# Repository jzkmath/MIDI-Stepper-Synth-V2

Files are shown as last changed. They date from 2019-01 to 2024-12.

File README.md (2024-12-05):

# MIDI-Stepper-Synth-V2
This is the Version 2 of my MIDI Stepper Synth. The key differences between this and Version 1 is
that this version uses the Terasic DE0-nano (Cyclone IV) FPGA as the controller instead of Arduino.
The key advantage to doing so is that an FPGA can execute commands at the same time instead of sequentially.
This also allows for a better understanding of how MIDI actually works, because the MIDI has to be decoded manually
instead of using a MIDI library.

This project is being performed at the Virginia Tech AMP Lab, and the project can be seen (Link is dead)

Alternatively, you can view the project documentation/Notes in the "Project Documentation" folder and opening the "Documentation.md" file.

**Please use the project page or PDF to see the BOM and all information on this project!!!**

Since MIDI uses a specific type of UART, the FPGA will take the serial data and convert it to parallel, as a 3 byte register.
Once this is done, the message is decoded such that the stepper motors react accordingly. 

## Basic MIDI Layout
The 3 byte MIDI Message is as Follows:
**1XXXCCCC 0NNNNNNN 0VVVVVVV**
- **X** - MIDI Command. This is 1000 for Note OFF, and 1001 for Note ON.
- **C** - MIDI Channel. 
- **N** - MIDI Note. This is the pitch that is specified. 60 for example is Middle C or C4.
- **V** - MIDI Velocity. This is similar to volume.

The general idea is that we want to turn the MIDI value into a stepper speed. To do this, we use a
similar method to how version 1 handles this, except this time we use clock cycles instead of time.
The DE0-nano has a 50 MHz clock, so we can generate a square wave at a specific frequency by counting
a certain number of clock cycles and toggling the state of a pin. 
The code simply takes the MIDI note value and converts it to the corresponding number of clock cycles
needed to do so.

In addition to the functions of version 1, version 2 also uses the velocity information to control 
how many steppers turn. The higher the velocity, the more stepper motors turn on (ranging from 0-4)
This is how the array of floppy drives work on the popular "Floppotron" on YouTube.

## Block Diagram
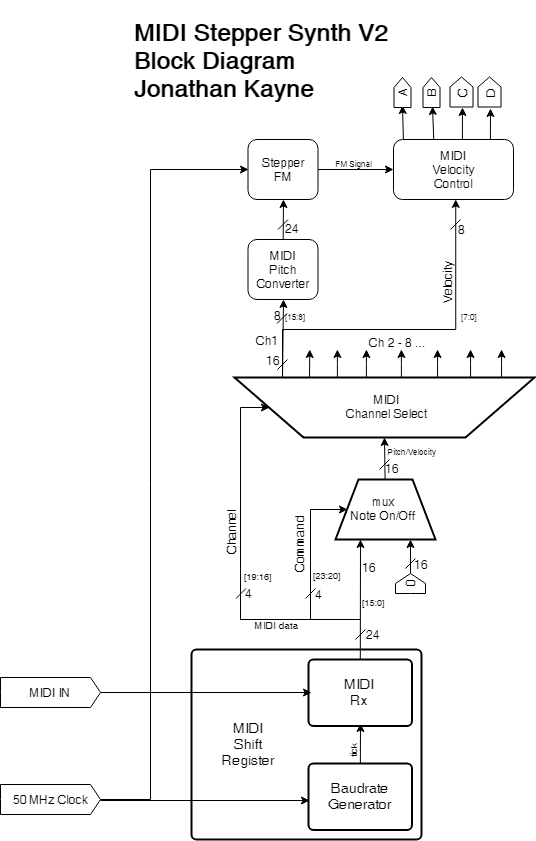
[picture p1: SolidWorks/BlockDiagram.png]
Block Diagram


## Principle of Operation
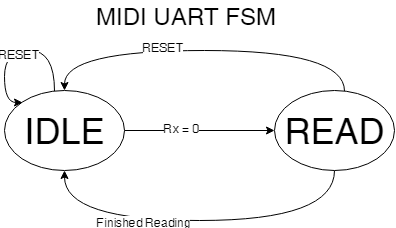
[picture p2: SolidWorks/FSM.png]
FSM


The first thing that must be done to convert MIDI into stepper music is that we need to decode the MIDI signal. MIDI uses 31250 baud UART (Universal Asynchronous Recieve Transmit) to send an recieve data. This is a form of serial, so we need to load this into a register to act upon with combinational logic. To do this, we use a Finite State Machine, or FSM with two states; Idle and Read. 
In the Idle state, the Rx line is high. When a device wants to send a message, the Rx line is dropped low. This is known as the start bit and the actual data is the 8 bits that follow, then the line goes high again (called the stop bit).

Knowing this, we can use the start bit as a means to change to the read state. 

In the read state, we want to look at the Rx line in the middle of each bit and shift that bit into our register. To do this, we count a certain number of clock cycles to get to the center of the bit. Given that the DE0-nano has a 50MHz clock and MIDI is 31250 baud, that means that it takes 800 clock cycles to get to the center of a bit, and 1600 clock cycles to go from center to center.

When the start bit is detected the read process is as follows:
1. count 800 clock cycles to get to the center of the start bit
2. count 1600 clock cycles to get to the center of the data bit
3. shift in the value of the Rx line
4. repeat steps 2 and 3 a total of 8 times
5. output the shifted value
6. wait for the Rx line to go high (stop bit detected) and go back to the Idle state.

Once we do that, we have our byte of data. Knowing that MIDI is 3 bytes of data, we take the byte and shift it into a larger, 3 byte register. After that, we can use combinational logic to control the stepper motors.

MIDI has a byte of control information (Command and Channel) and two bytes of data (Pitch and Velocity). We want to use the first byte to properly route the last two bytes appropriately. To do this, we have a single data router module and register modules for each channel. The registers have an enable and clear control signal and will either load or clear their contents depending on which input is pulled high. The second and third bytes are connected to the inputs of all the registers via a common bus and the first byte is used by the router module to control which register gets enable or clear pulled high. Note on (1001) or Note Off (1000) determines whether the register is enabled or cleared, and the channel determines which channel this happens to.

Once the register has the data, we need to convert the pitch into clock cycles. We look at the pitch value and corresponding frequency. We then figure out how many clock cycles elapse in half the period of the note. We do half because we want to create a square wave, which has a 50% duty cycle.

Using the converted value, we have a module count up to that value and then toggle the state of the pin. This is the equivalent to the "Blink without delay" sketch that is used in Arduinos (except for FPGAs).

Finally, we use the velocity value to determine how many stepper motors get that signal, which can be anywhere between 0 and 4.

## Credits
The basic UART decoding Verilog code is based off code provided by Electronoobs, modified to be more stable and work with MIDI.

Special Thanks to Robert Perkel and Bob Lineberry for helping with this project and providing assistance with this.

## Legal
This project is under the GNU GPL3.0 Open Source License. 
You are free to use the code in your project, so long as you credit the creator (Jonathan Kayne).
I want people to be able to use my code, but I don't want people to plagiarize my work!

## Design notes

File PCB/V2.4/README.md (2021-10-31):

### Stepper Synth V2.4

This is the Final Revision of the MIDI Stepper Synth V2 PCBs. They were designed in Eagle, and rendered in KiCAD.

I added new connectors and changed the header sockets to be in a zigzag pattern so that they would be easier to solder.

## Interface PCB
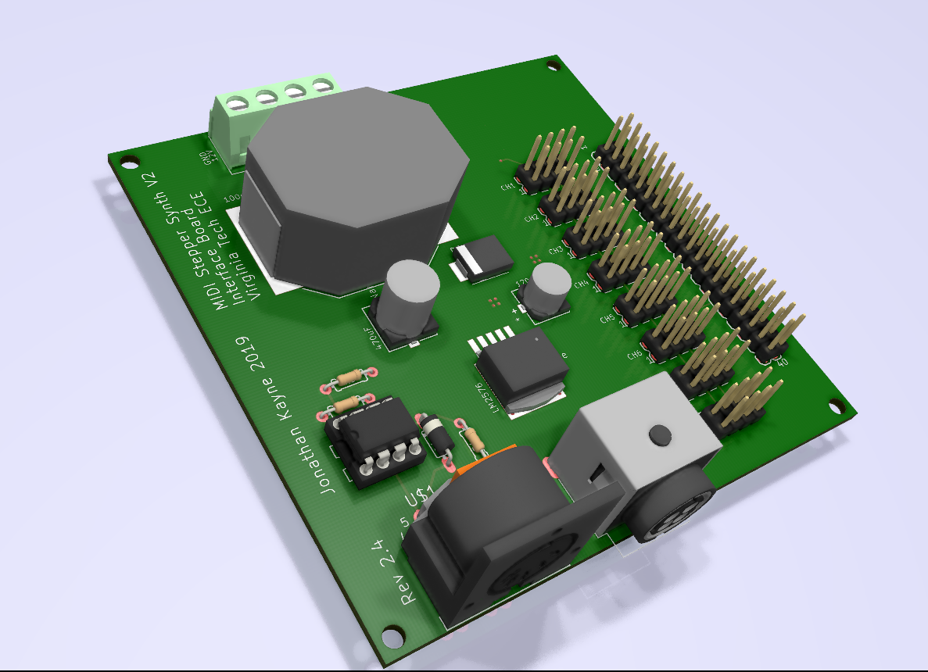
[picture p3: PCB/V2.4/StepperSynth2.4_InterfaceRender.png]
Interface


## Motor PCB
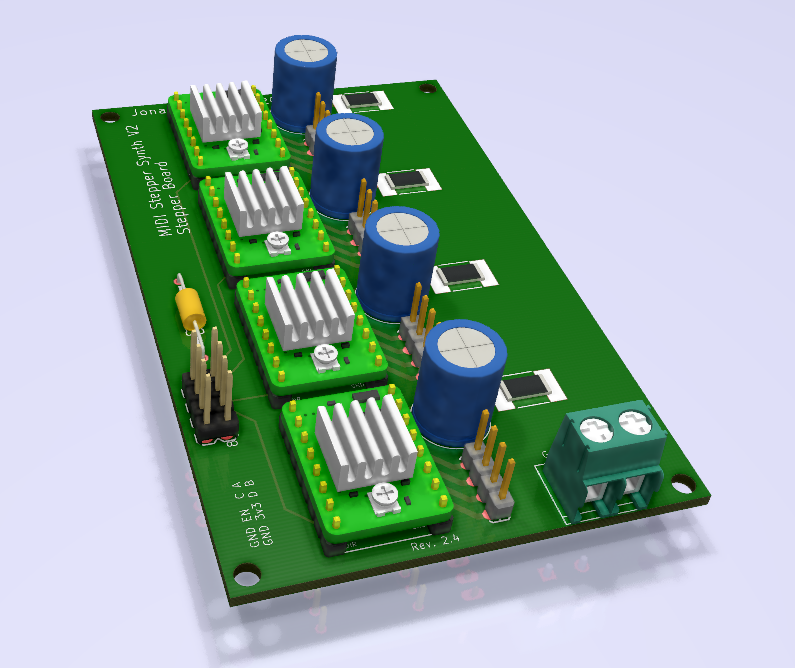
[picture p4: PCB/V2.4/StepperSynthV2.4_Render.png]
Motor


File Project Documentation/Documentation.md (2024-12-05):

# MIDI Stepper Synth V2

## By: Jonathan Kayne, Virginia Tech Class of 2021

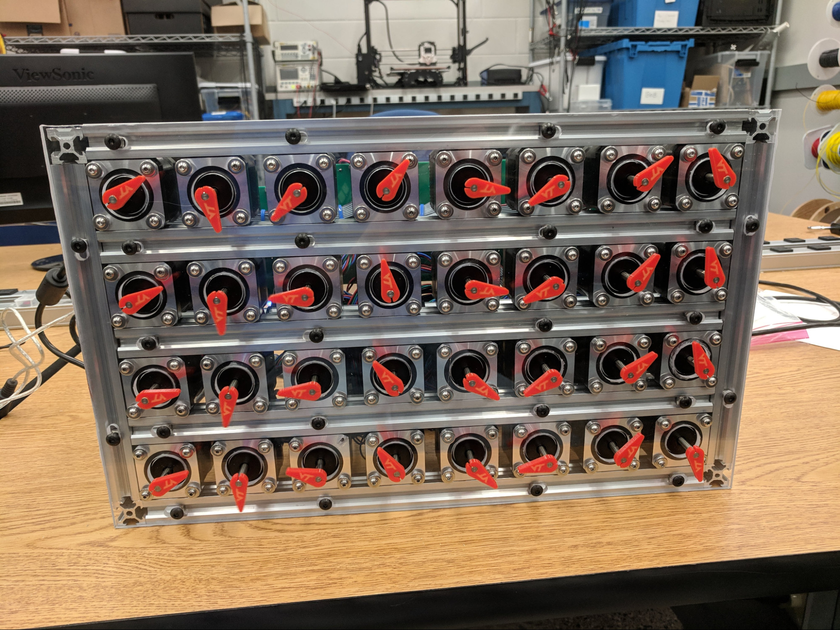
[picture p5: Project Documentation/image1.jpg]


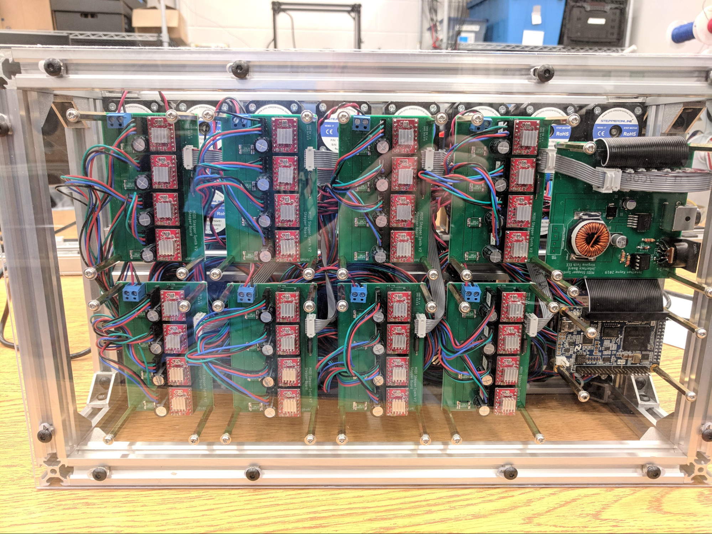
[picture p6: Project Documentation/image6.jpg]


## Project Overview

This will be a continuation of a project I designed in the spring of 2018 on my own. The stepper synth uses MIDI data to "Play" stepper motors. Stepper motors often create a hum that is dependent on the speed that the motor is spinning at. By writing music and sending it to the stepper synth, you get a song. The original stepper synth used 4 NEMA-17 Bipolar stepper motors, an Arduino Uno, and a CNC shield to drive the steppers.

This design works, but can be improved by adding more steppers and other instruments. Furthermore, use of an FPGA will allow for a faster processing time and more stable MIDI processing.

Optionally, an array of LEDs could be used with some filtering to light up depending on the frequency being played at any time.

## Tasks

* Choose appropriate FPGA

* Come up with a plan for the program.

## Educational Value Added

I have very little experience in FPGAs and verilog. Doing this project will allow me to learn procedural verilog as well as get a more in depth view of the MIDI protocol.

## Design Decisions

The MIDI stepper Synth will use an array of 8x4 Bipolar stepper motors (likely NEMA 17). These will be broken into 8 MIDI channels with 4 motors per channel. Use of 4 stepper motors will allow for variation in volume level, by changing the number of motors running.

## Design Misc.

Other information about the design, parts used, etc.

* The stepper motors are driven by the Allegro A4988 Stepper Motor driver module. These drivers contain two main control pins; Step and Direction. Direction controls whether the motor spin clockwise or counterclockwise, and Step advances the motor forward by 1 step upon the rising edge of a pulse signal. The frequency of the pulses sent to the step pin control the speed at which the motor turns. It just so happens that the frequency also corresponds to the audio tone that the motor produces. For example, if I were to put a 440 Hz square wave into the step pin, the stepper would produce an A4 note (440 Hz is a common frequency used for instrument tuning!).
* Musical Instrument Data Interface (MIDI) is essentially a version of serial (RS232) at a specific baud rate. Within the protocol, there are two messages that we are concerned with; "note on" and "note off". These messages are 3 bytes long, and contain the control signal, the channel, the note value (frequency) and the velocity (volume).
* The general idea for what the FPGA needs to do is to take the midi data and produce a clock signal whose frequency is dependent on the note value. These signals need to be independent of each other and only get changed when another MIDI message overwrites it, so a note will stay the same until either a new note value is given or the note off message is received.

## Parts

* 32x NEMA 17 Stepper Motors
* 32x A4988 Stepper Motor drivers
* FPGA
* 3.3v to 5v level shifter (for communication between the FPGA and A4988)

## Steps documenting your design process

### Thing 1

The general idea of what this device does is takes MIDI data and converts that into a pulse whose frequency matches that of the stepper motor. To do this, the MIDI must first be interpreted and acted on accordingly.

MIDI is a special version of serial communication (RS232). It runs at 31250 baud.

MIDI will hold the signal high until a message needs to be sent. When this occurs, the line is dropped low for a single bit. This is called the start bit.

The MIDI messages we are interested in are 3 bytes in length. The Message is as follows: "CCCCNNNN 0KKKKKKK 0VVVVVVV" where

* C = Command; 1000 = Note OFF, 1001 = Note ON
* N = Channel; ranging from 0-15, for channels 1-16
* K = Note Value; the value 60 corresponds to C4 (middle C)
* V = Note Velocity; how loud the note is

The note value will drive the frequency of the pulses for a respective channel. The velocity will control how many stepper motors receive that pulse, where 0 = none, 1-31 = 1 motor, 32-63 = 2 motors, 64-95 = 3 motors, 96-127 = 4 motors. This might be changed if the range is too broad. It should be such that the motors respond to certain dynamic levels; from pianissimo (pp) to fortissimo (ff)

A midi channel does not change its value until another message overwrites it. So if a note on message is sent, that note stays on until either a new note on changes the value (creating a slur) or a note off message is sent.

The FPGA will have registers that hold the current note and velocity values for each channel. The data will come from a multiplexer that is controlled by the N bits. This is so the data that is loaded in can be routed to the appropriate register.

In the event of a note off message, the multiplexer will output a zero for both note and velocity.

If at all possible, an enable timeout feature should be implemented for the stepper motor control. The A4988 has an enable line that can be used to enable/disable the steppers. When enabled, the steppers have current supplied to them, which causes them to heat up (and waste energy!). When the device has been inactive for a certain amount of time, pull the enable line high.

### Thing 2

Information on the A4988 Stepper Driver. Here is a picture of the pinout for the A4988:

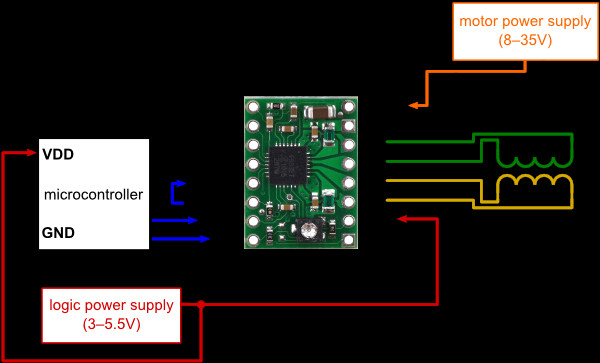
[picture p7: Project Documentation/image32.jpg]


The ENABLE line enables the driver when it is set to a logic low.

MS1-3 are the Microstepping mode controls. You can increase the resolution by changing the state of these pins (full step, half, quarter, eighth, and 16th). This doesn't matter for this project so they will be all driven low (full step mode). 

### (Preliminary Schematic)

**12/7/18:**  The schematic and board were created in Autodesk Eagle. The schematic and board are as follows:

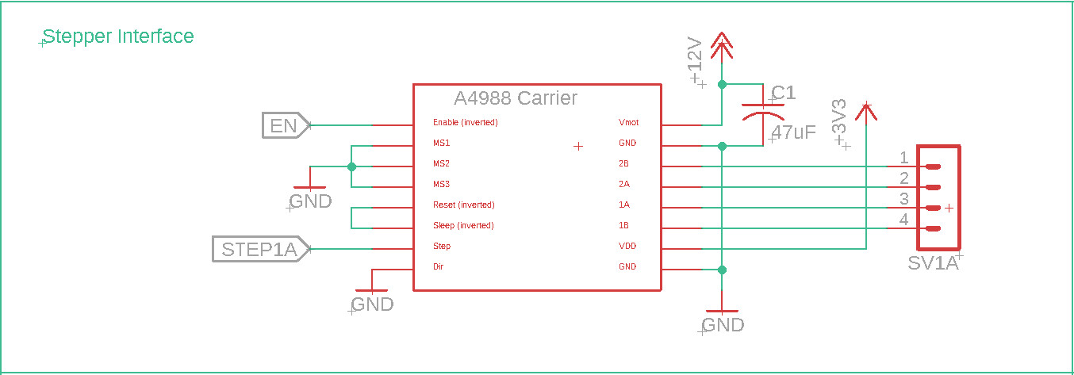
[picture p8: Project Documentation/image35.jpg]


The 47uF capacitor is there to prevent large voltage spikes from damaging the motor drivers. Looking at the Arduino CNC shield showed that each driver got its own capacitor.

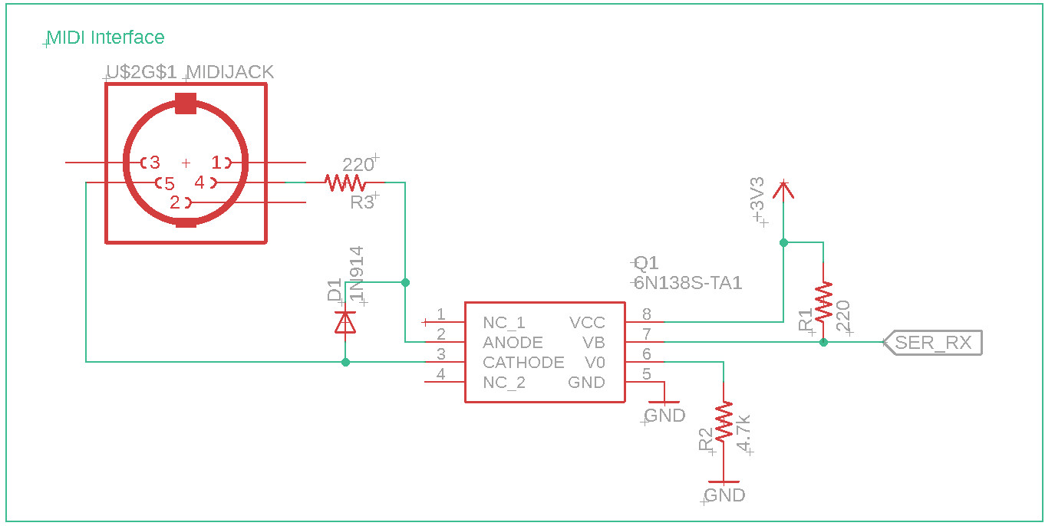
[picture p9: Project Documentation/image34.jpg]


The 6N138 is an optoisolator IC chip. MIDI uses a 5V communication method while the DE0 nano uses 3.3V. It is common to use an optoisolator to isolate the MIDI signal between the devices. It should also be noted that the ground connection on the DIN connector is left floating to prevent ground loops from occurring along the shield of the MIDI cable. The diode is for reverse polarity protection. The 4.7k resistor acts as a bleed resistor. This is due to the fact that stray charges can build up on the phototransistor, which can increase the propagation delay. The resistor fixes this. 

This is based off a tutorial by ["Notes and Volts" on YouTube.](https://www.youtube.com/watch?v=0L7WAMFWSgY)

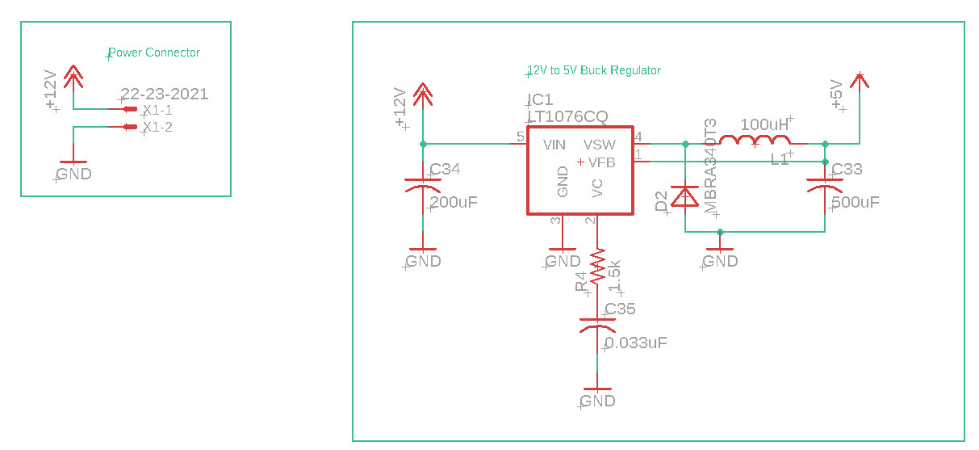
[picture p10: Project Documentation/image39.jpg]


This uses the LT1076 as a buck converter for converting the 12V to 5V to power the DE0 nano FPGA.

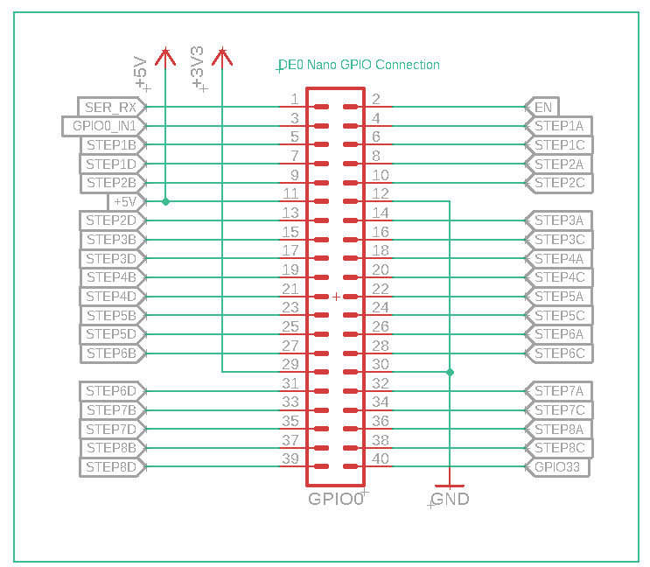
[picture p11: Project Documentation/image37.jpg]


## Verilog Works!
**12/13/18** - The Verilog code has been created and tested and now successfully works!

The main challenge to getting this to work was in the MIDI Shift Register, as MIDI uses a form of UART (Universal Asynchronous Receive Transmit). This means that there is no clock to keep things in sync. The solution is to use what is known as a Finite State Machine (FSM). The way the shift register pulls in data is done by creating a clock that is 16x faster than the specified baud rate (in this case 31250 bps) and then having two states: Idle and Read. The module sits in the Idle state until the serial line falls low, indicating the start bit. This puts the module into the read state. 

In the read state, the module counts 8 ticks (the clock that's 16x faster than our baud rate). At this point we are in the middle of the start bit. After this, we count another 16 ticks and record the value of the serial line. This is repeated for all the 8 bits, where the bits are shifted into a register. Afterwards, the module goes back into the idle state. 

Since there are 3 bytes of MIDI data, there is another shift register that shifts each byte in as it is received.  

After the bits are properly shifted in, the values are processed and sent where they need to be. The first thing that is analyzed is the command, which is either a note on (1001) or a note off (1000). The is a 2x1 multiplexer that either passes the pitch and velocity through if the value is a note on, and passes a zero through if the value is note off or anything else.

After that, the pitch and velocity go into a demultiplexer that sends the pitch and velocity to their intended MIDI channel. The specified channel is located in the last 4 bits of the first byte.

For each channel there are 3 modules: a pitch value converter, a frequency modulator, and a velocity controller. The pitch value converter takes the MIDI note value and converts it to a number that equates to the number of clock cycles needed for half the period of the intended frequency, since we want to produce a square wave. Since the clock is 50 MHz, you can calculate the number of clock cycles needed by 50 MHz / (2 * pitchFrequency). 

The converted value is then sent to the frequency modulator, which simply counts up to the specified number of clock cycles and toggles the state of a register. (essentially this is the same code used to blink an LED on an FPGA)

This signal is then sent to the velocity controller, which passes the signal to 0, 1, 2, 3, or 4 stepper motors depending on the velocity value given, where 0 is none, 1 - 31 is one motor, 32 - 63 is two, 64 - 95 is three, and 96 - 127 is four (all).

The block diagram is as follows. I have also added the verilog code, which is in the "files" section!

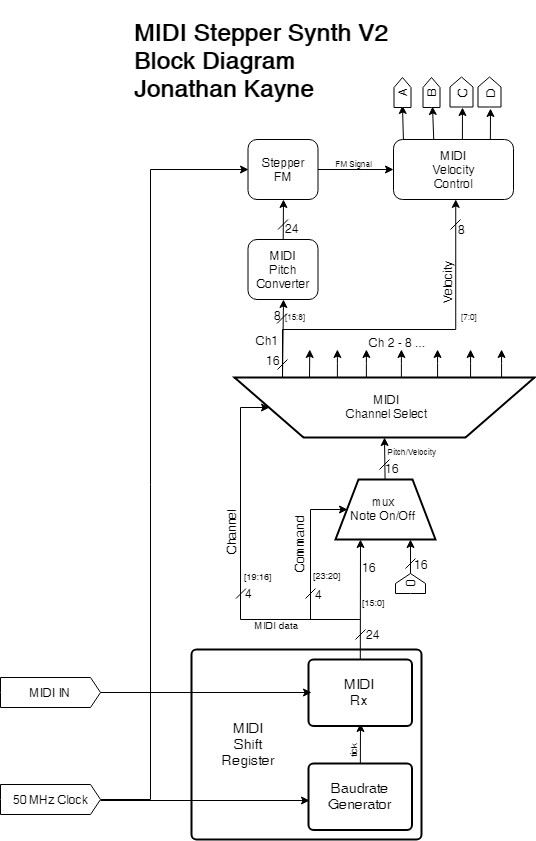
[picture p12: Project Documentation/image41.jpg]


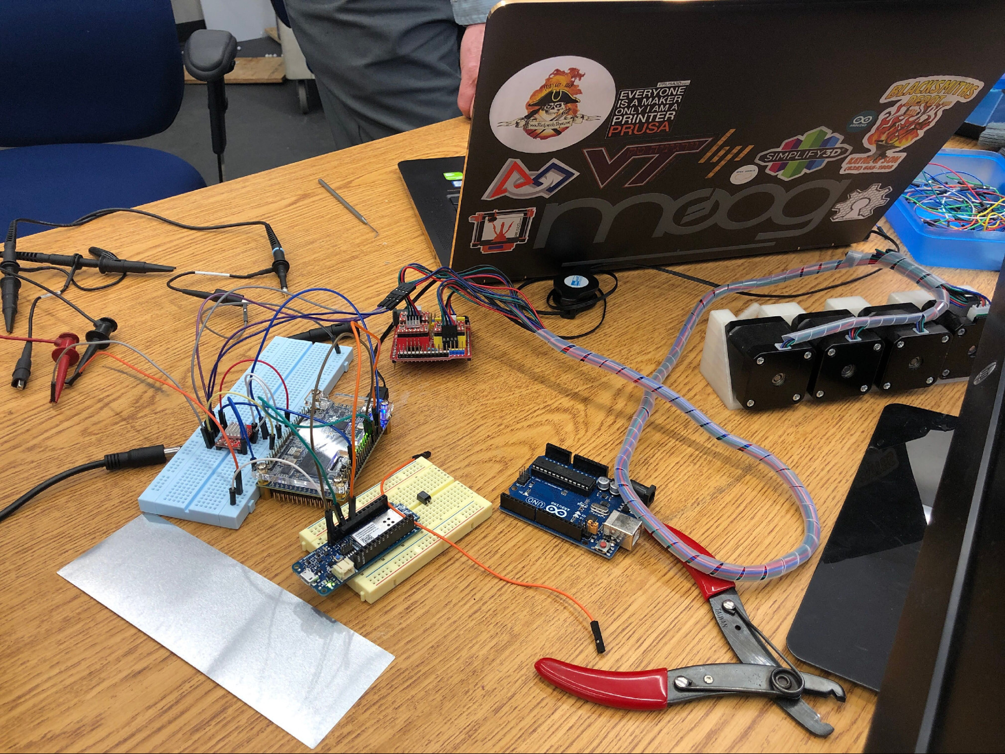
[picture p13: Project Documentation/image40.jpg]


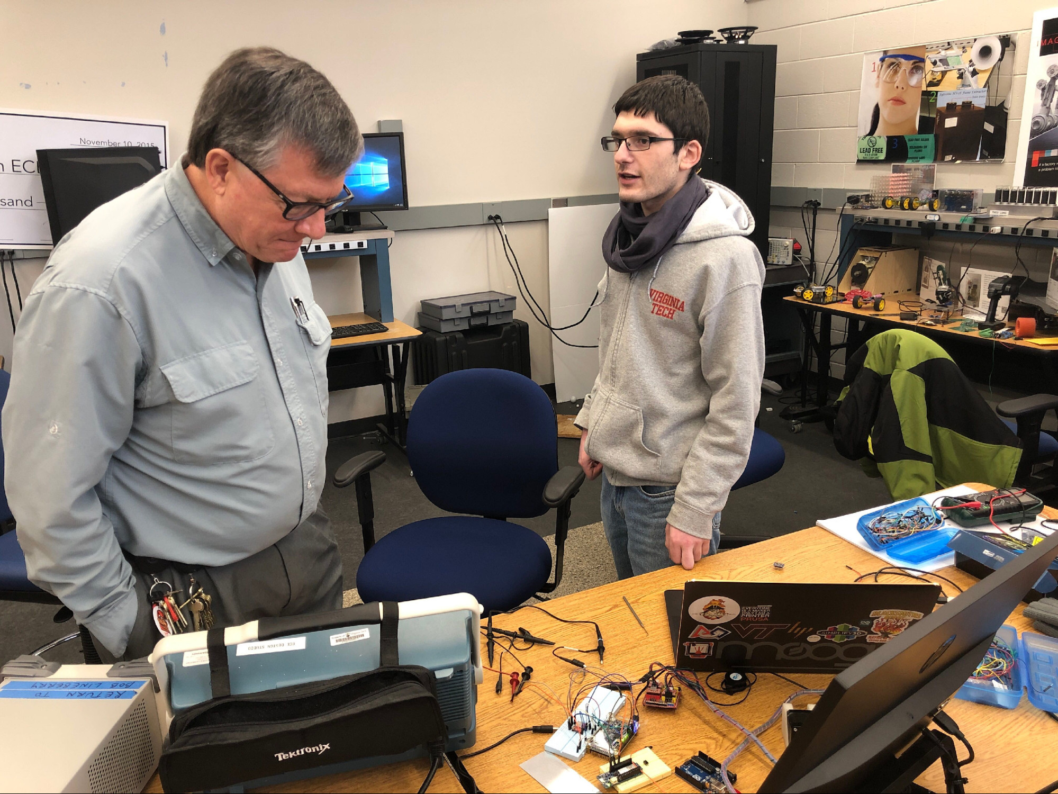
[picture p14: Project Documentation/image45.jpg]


I also plan on redoing the PCB design to make it more modular and so that it can handle the high current that running 32 steppers causes. There will be two modules: a Stepper Channel Module and the Controller Module. The Stepper Channel module will drive 1 channel of 4 stepper motors. There will be 8 of these. The Controller module will hold the MIDI interface and the DE0-nano interface with the buck converter.   

## Schematics 2.2 

**12/21/18** - created new schematics and PCBs to be used in the stepper synth, as well as updated the BOM. I used an online software called EasyEDA to design the boards. It has a much simpler user interface and integrated libraries that make it much easier to use than Eagle. Also, it has a built in export to Gerber option that makes sending to board houses easier. I will be using SeeedStudio to make the boards by recommendation of peers and the fact that the AMP lab has prior experience with them. Here are some pictures of the new schematics and PCB layouts:

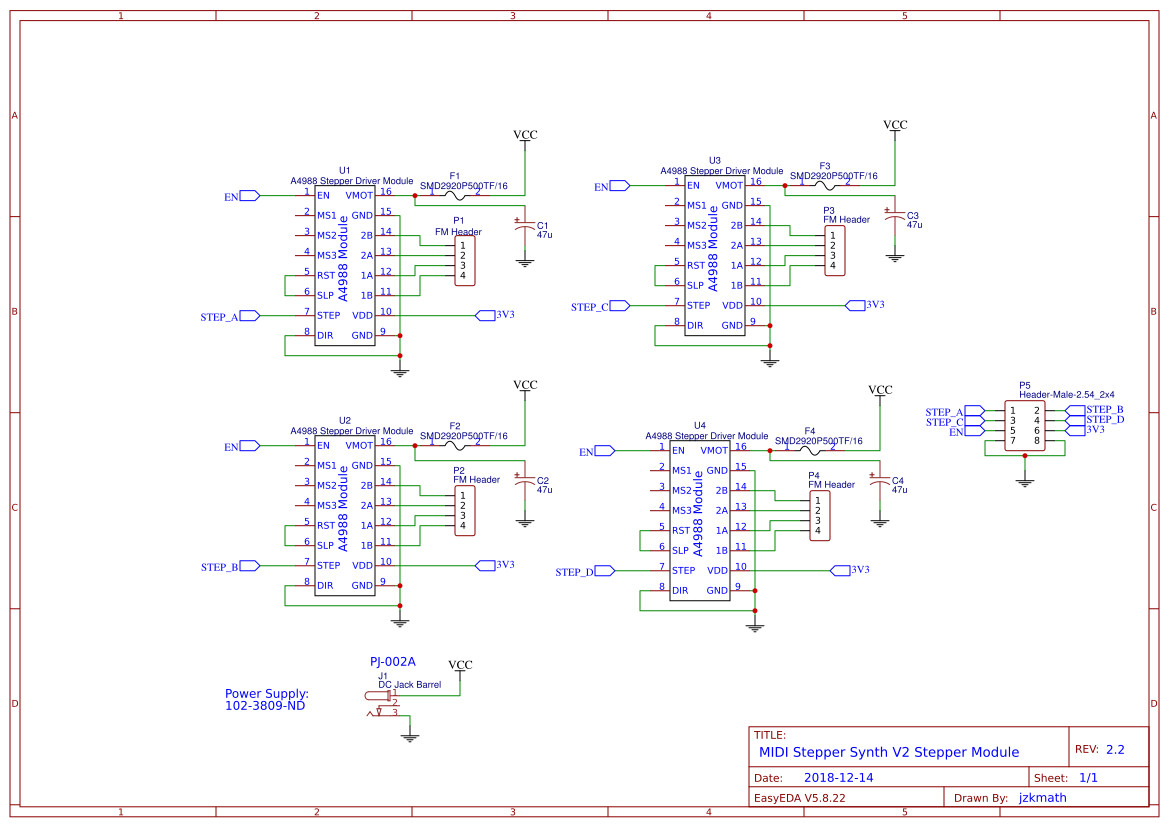
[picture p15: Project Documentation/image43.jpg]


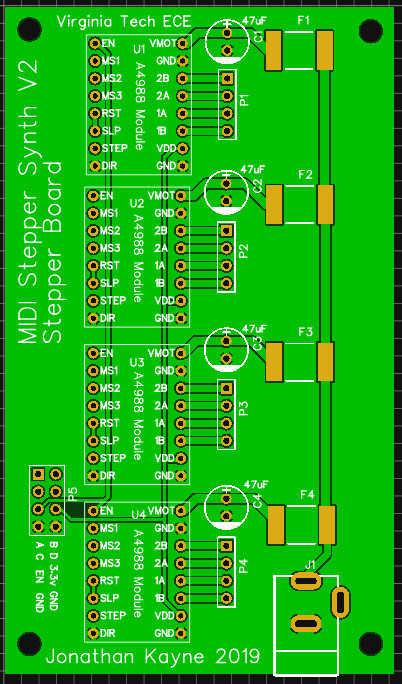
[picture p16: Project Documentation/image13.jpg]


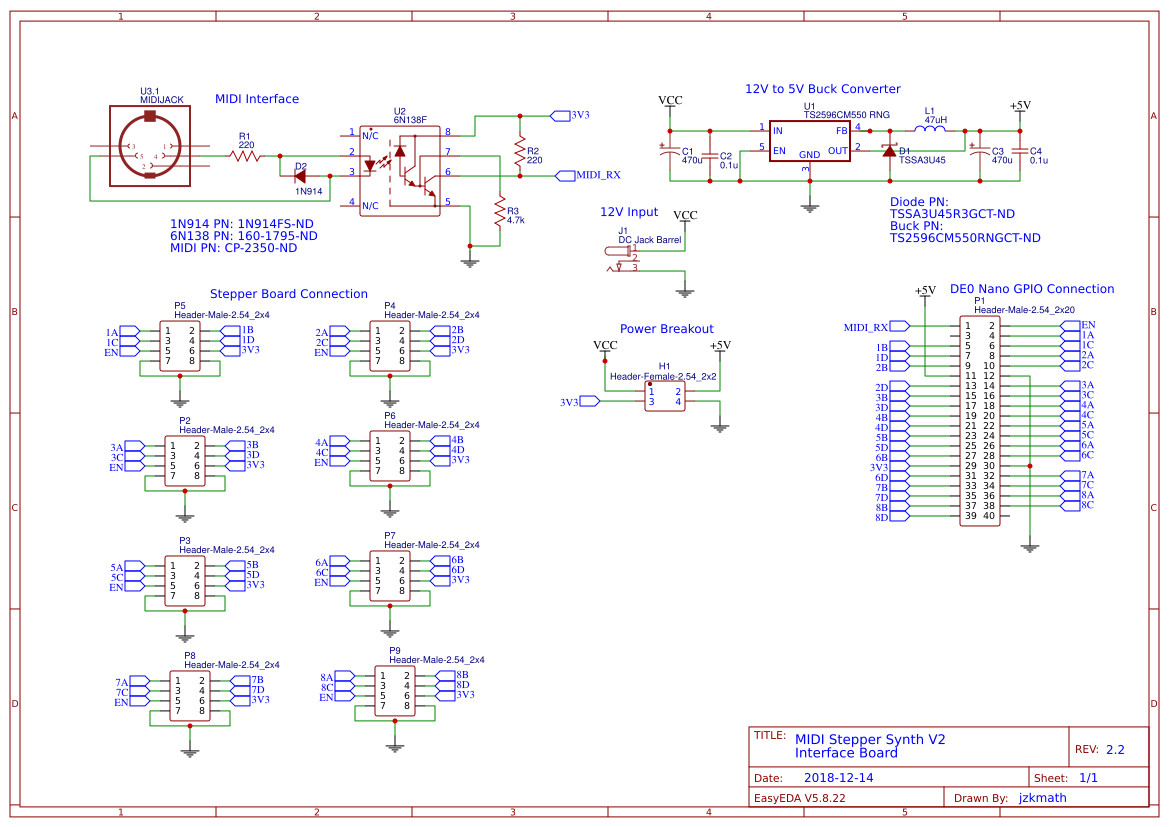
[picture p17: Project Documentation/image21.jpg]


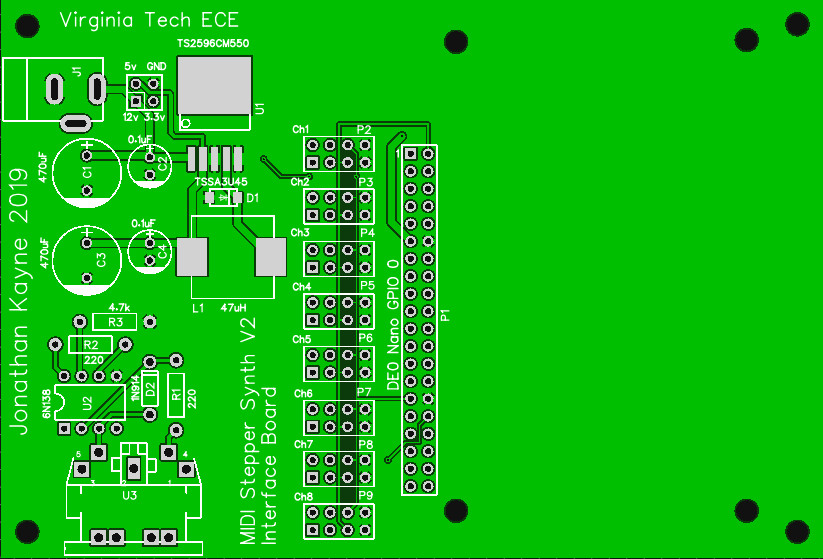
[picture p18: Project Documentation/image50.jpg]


## Schematics 2.3

**1/13/19** - There were some issues with the design of the two PCBs, so they were redesigned in Eagle. The main issue was the fact that the buck converter used an odd IC chip. In the redesign a chip made by TI was used, and the parts were selected using TI's web-bench. This also gave me a chance to learn how to make my own libraries in Eagle, as importing some of the components from Digikey can look odd in schematic view. Furthermore, the motor ground and digital ground are isolated in the new Motor PCB, being connected via a ferrite bead. Also, the boards have a uniform size in millimeters, so layout is simpler.

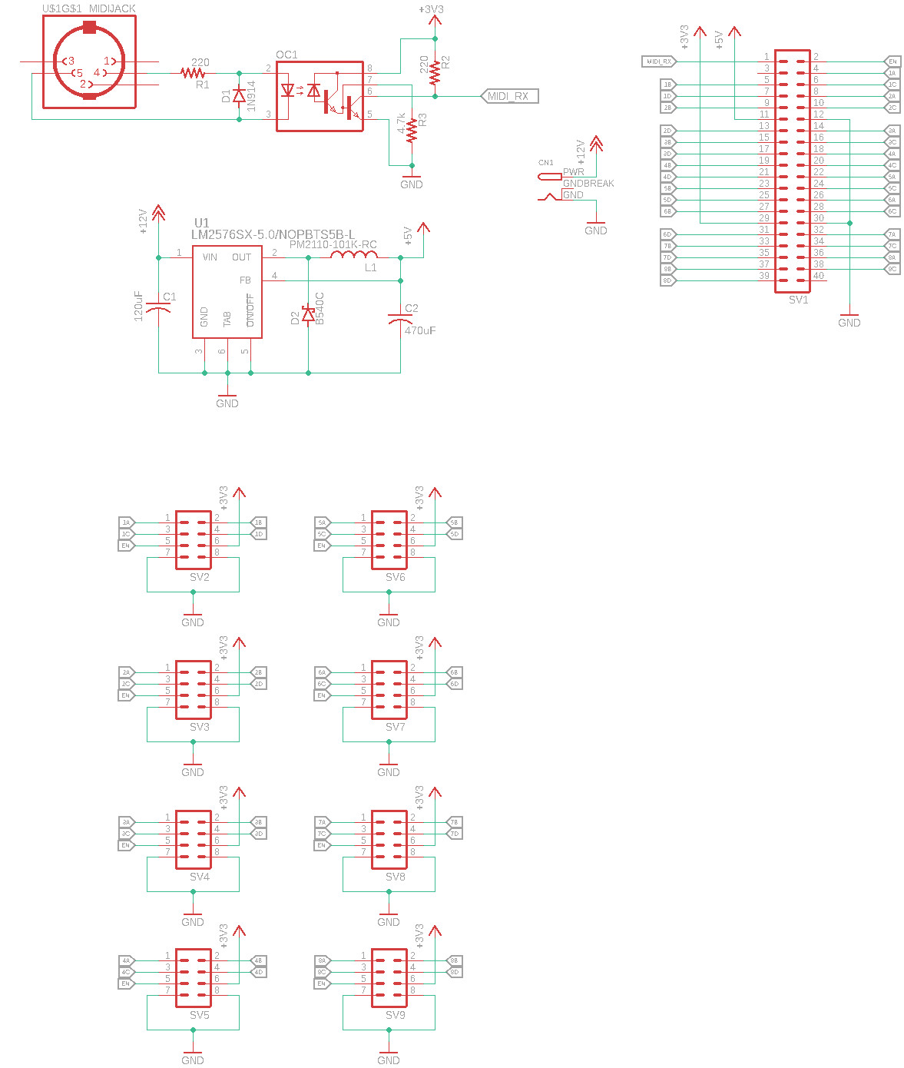
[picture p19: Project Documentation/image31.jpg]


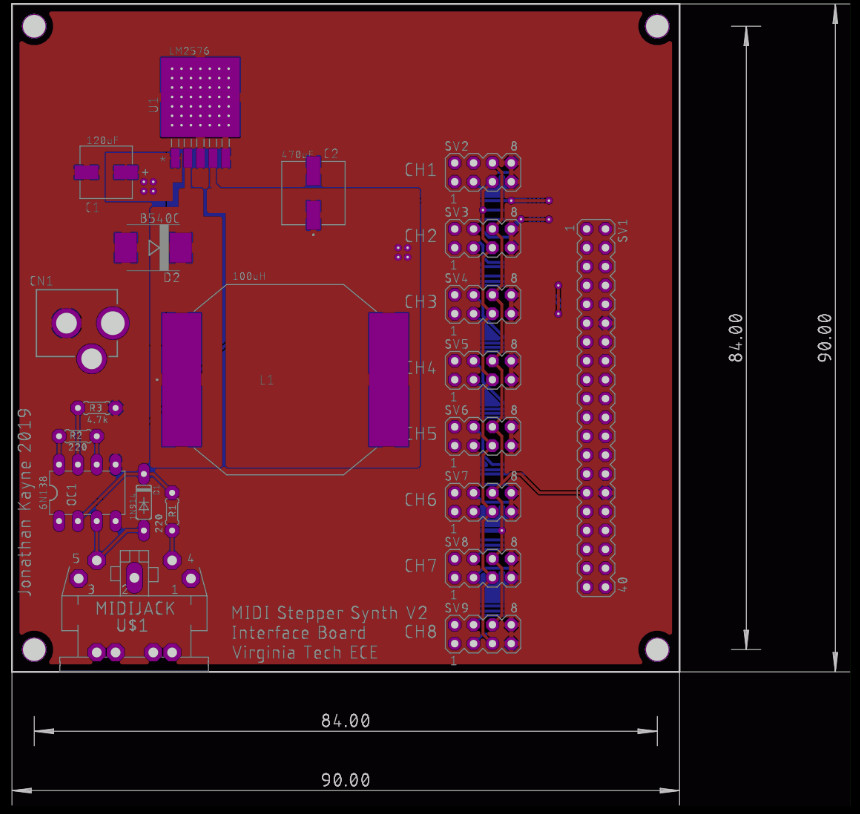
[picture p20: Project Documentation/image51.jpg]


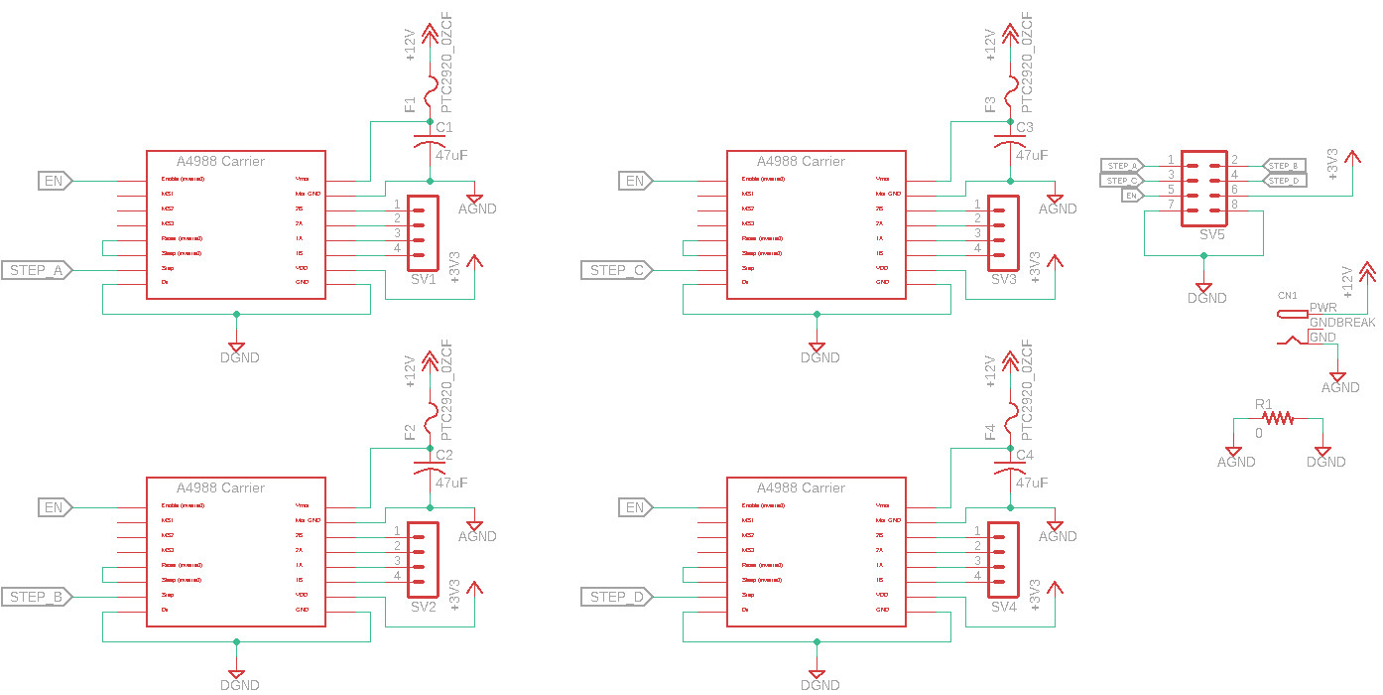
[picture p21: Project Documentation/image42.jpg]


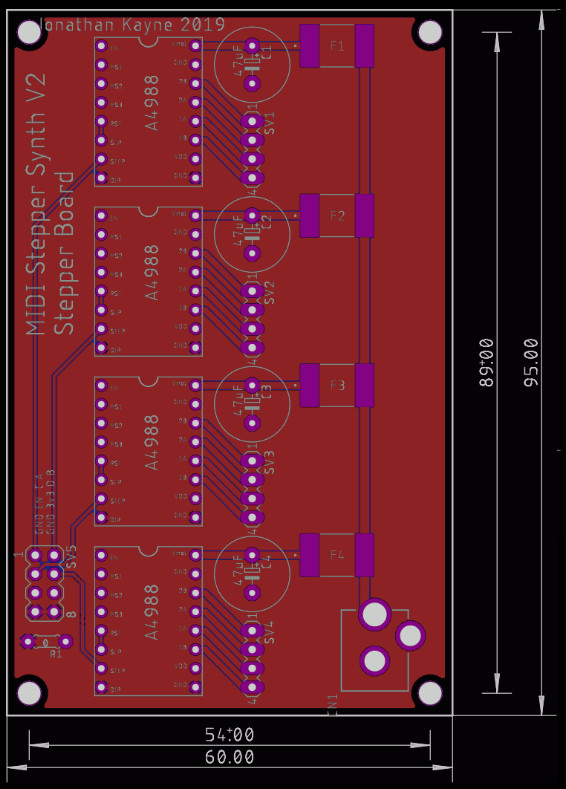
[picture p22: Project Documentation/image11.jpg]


## BOM Update and MIDI Creation Workflow

**1/16/19** - The mechanical BOM was created and I have also made a few MIDI files for the synth. I thought I would go over my procedure for creating MIDI files and parsing them to the stepper synth. The two programs I use for this is MuseScore 3 and Ableton Live 9. MuseScore is a free, open-source music notation software that I have been using for about 8 years for both music composition and band sheet music creation. 

The general idea is that I want to create 8 staves each with a monophonic track. For those who don't read music, stave is the plural of a staff. The staff consists of 5 horizontal lines and is where we place notes in music. The head of the note lies either on a line or between the lines and tells you the pitch depending on the clef (treble, bass, alto or tenor) and the duration depending on the shape (whole, half, quarter, eighth, etc). The term monophonic means one note at a time. Examples of monophonic instruments include most wind instruments like a saxophone (which is the best instrument ever and is why I play it ;) ). The opposite of monophonic would be polyphonic, which would be like a piano, which can play multiple notes simultaneously (referred to as chords). 

The way I normally get the songs is by going to MuseScore.com and finding a song premade and then modifying it to work for my synth. Often there will be chords in the music, so what I often do is move the chord to an empty staff and use the explode command (Tools > Explode) and the chord will be split across the empty staves below. After creating the song, I export the song as a MIDI file (.mid) and then move onto Ableton. Note that I could just use the jack plugin that is built into MuseScore to play the MIDI file to the synth, but I find that it doesn't send the Note Off command if you press pause which Ableton does.

Ableton Live is what is known as a Digital Audio Workstation (DAW), and is one of the popular DAWs used in the music production industry along with FL Studio and Pro-Tools. In Ableton, I created a template called "StepperV2.als" that contains 16 MIDI tracks. The first 8 hold the MIDI data and send the MIDI to the stepper synth. The other 8 have a simple saw-tooth instrument attached and simply play what is in the first 8 tracks. These are only used for testing and are muted when the synth is playing. Channels 1-8 will have the "MIDI To" set to the USB MIDI controller and their respective channels set. When I want to create a song, I simply drag the MIDI file created in MuseScore into the timeline and I am good to go! I should also point out that I have been putting the converted MIDI files onto the GitHub for this project. Below is a screenshot of playback of "Enter Sandman" on Ableton. Why "Enter Sandman"? Because this is Virginia Tech!

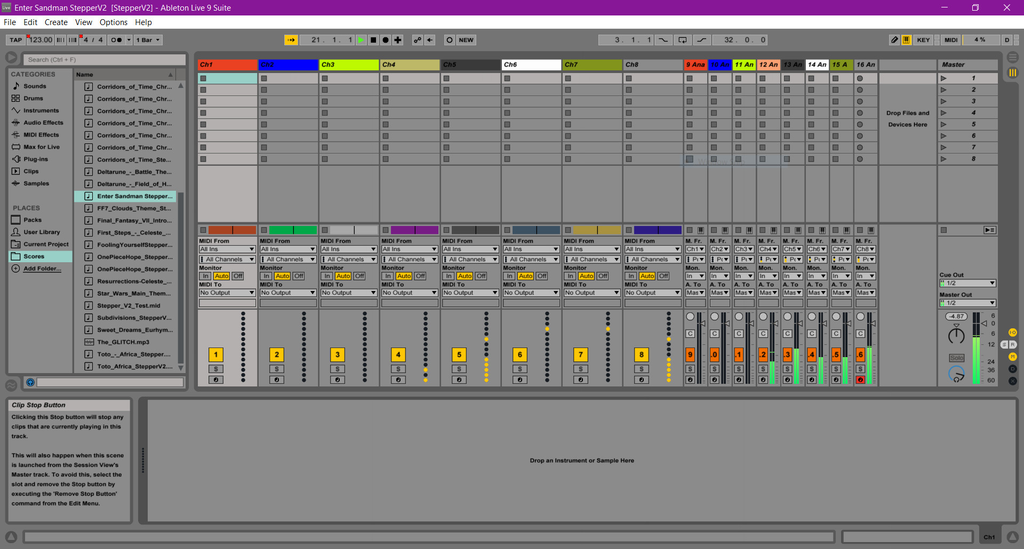
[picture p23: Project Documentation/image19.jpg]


## Mechanical Assemblies

**1/28/19** - It seems that most of the components are in to assemble the Stepper Synth, except for the PCBs and the stepper Motors. I decided that I want to discuss some of the mechanical build for the instrument.

I designed the assembly in SolidWorks Student Edition 2017, as I have a lot of experience with this CAD software (and a CSWA in it too). Being that this is meant to show off the stepper motors, I wanted to ensure that the motors and circuitry is visible to the public. This was achieved by using clear acrylic sheet and aluminum extrusions. By using 2020 aluminum extrusions, I can maximize rigidity while minimizing the overall weight. I should point out that Stepper Motors are heavy items, so 32 of them makes for a rather heavy instrument (about 40 pounds!). Because of this, I decided to put horizontal braces between the motors to improve rigidity. I just didn't feel comfortable having 40 pounds of weight on a single panel. Also, adding these braces adds contact area to the motors which helps with acoustic performance!

On the other side, I put another acrylic panel with holes and standoffs for the PCBs. Honestly I like circuit boards and simply wanted to show off my soldering and PCBs that I designed! Also, I think it adds to the vibe I am trying to create with the whole aesthetic of the instrument. Plus, the LED's on the DE0-nano FPGA would be visible.

In the center of the assembly between the boards and motors is two cross-braces that are meant to be mounting points for the 9 power supplies that are needed to power each PCB. It also adds points for creating wiring harnesses. I really want the wiring to look neat and professional. (Did you know I have the nickname "Ziptie"?)

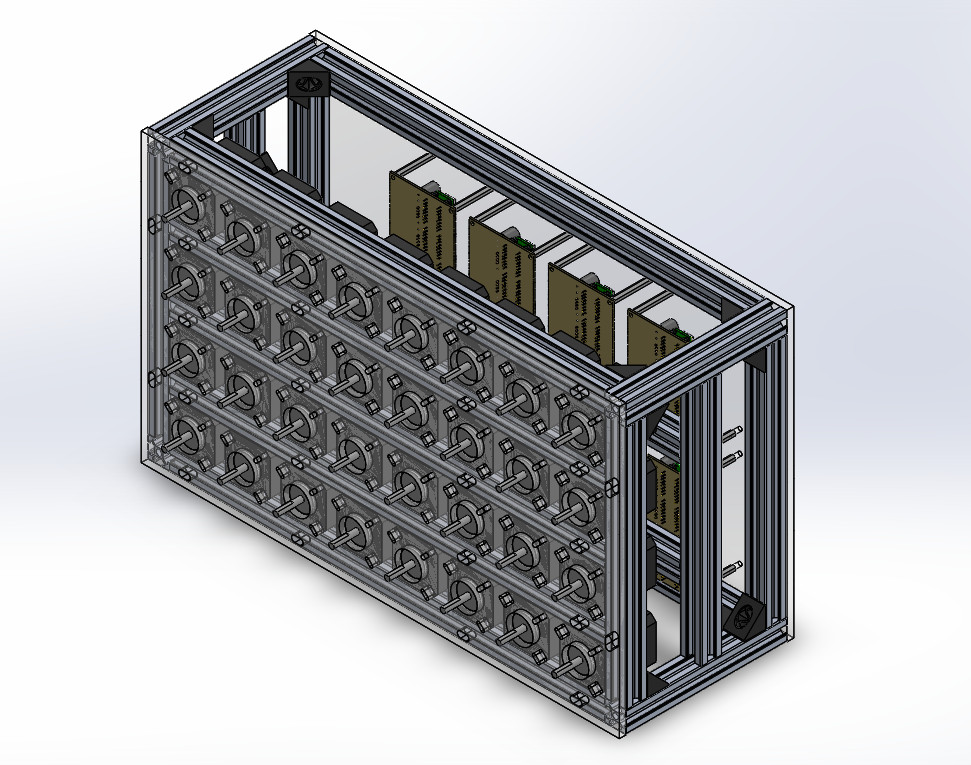
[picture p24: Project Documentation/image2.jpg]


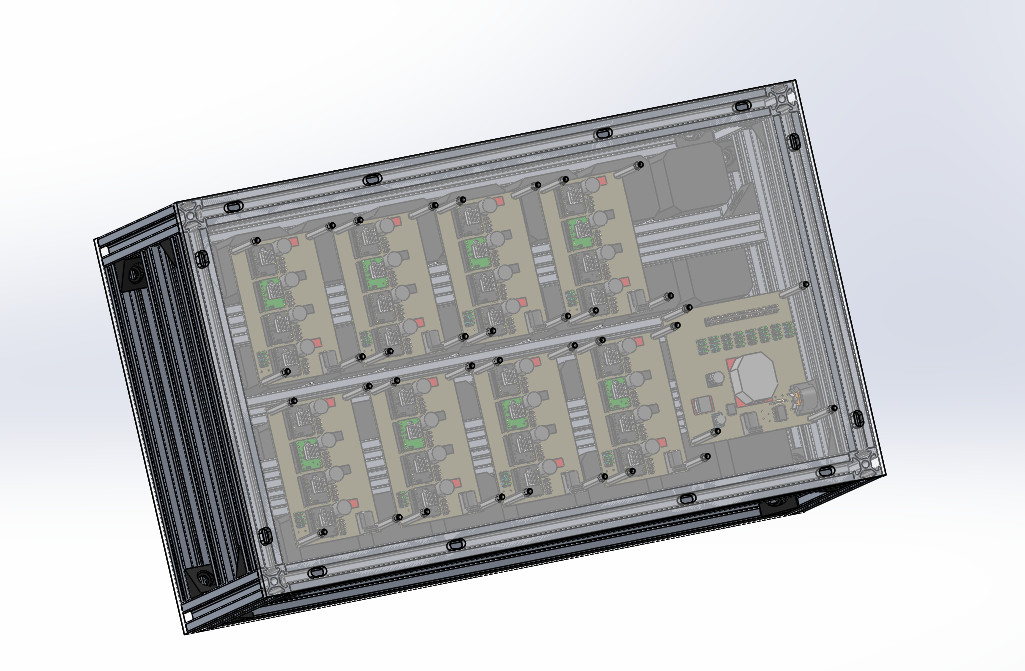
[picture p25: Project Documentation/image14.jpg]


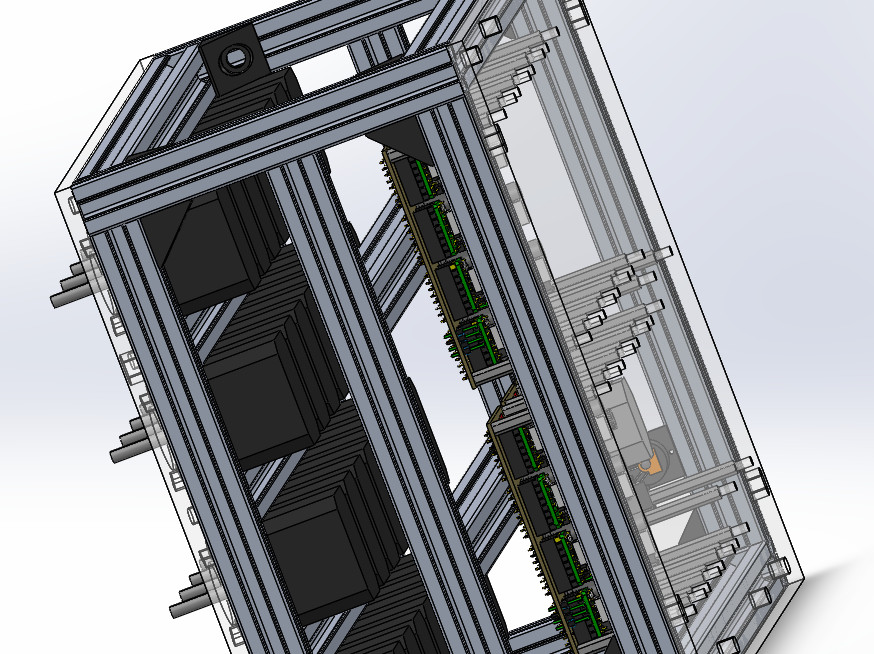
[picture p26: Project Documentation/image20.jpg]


## Begin Assembly!
    
**2/1/2019** - The PCBs and electrical components came in, so I was finally able to start assembly of the Synth. To make sure that the power supplies would work with the board, we only purchased two and I assembled one of each board. After building the PCBs, we hooked up the power supplies, installed the A4988 stepper driver modules, and attempted to adjust the current on the board, which was much more difficult with these cheap boards than expected. Normally, you can check the current limit by adjusting the potentiometer and connecting a multimeter to your screwdriver as you adjust the voltage. There are two sense resistors on the module, and the voltage you want to see is as follows:



We weren't able to get the multimeter to give us an accurate voltage measurement, but fortunately it is not very important, because these stepper motors don't draw a lot of current unless they are put under a load, which they won't. Therefore we just set the current limit to the max.

Once we set up the connections, I found that it wasn't working in a coherent manner. After looking at the MIDI line through an oscilloscope, I found that Ableton was the culprit, not the stepper synth. The FPGA expects only note on or note off messages, so anything else could make the system unstable. I found that it was sending a MIDI clock message, which was covering up the important information. When using Ableton, in the device configuration menu, only the output "Track" should be on. "Sync" and "Remote" should be off and the Input disabled. Doing this fixed it and I managed to get the synth to play "Flight of the Bumblebee" and a little of the "Imperial March" to test.

Now that we know that the power supplies work, and that a single channel works, the rest of the power supplies can be purchased and the boards assembled. I forsee this machine being fully functional in the upcoming weeks, once the mechanical parts come in!











## More Soldering and Assembly Difficulties

**2/2/2019** - Work was really slow today so I got to leave a little bit early. I used the extra time to solder up the 7 remaining Stepper PCBs. I managed to get into a groove and all of them assembled well. The only real hiccup was that one of the 47uF capacitors ended up having a lead get pulled out. It was probably my fault, but when removing electrolytic capacitors from the tape real, don't pull on them like I did, or the leads might get pulled out. For that one capacitor, I had to use one of the capacitors from the component cabinets as a substitute. I put that capacitor in channel D so that it would be used the least (channel A gets used for all notes, and D is used only for notes with a velocity of 96-127). 

One other thing that I (and Dr. Lineberry) should point out is that I should have ordered header pins with the zigzag bend at their base so that they stay in the board when you flip it over to solder. It made assembly much more difficult. I would use my brush to keep the PCB flat as I soldered a single pin, and then use my finger to readjust the header so that its flat against the board. 

Another thing I wanted to mention was that I attempted to figure out the cable length for the ribbon cables used between the boards. SolidWorks has this nifty tool called routing, where you can route wires in the assembly and then "flatten" the cable to get cable lengths. Unfortunately my computer was having a hard time doing this and the connectors weren't behaving as expected. The videos showing the process make it look super easy, but it just wouldn't work. Therefore, I think it would be better for me to just wait until my mechanical parts come in and figure out cable lengths the old fashioned way. If I really wanted to, I could print out the DXF of the back panel layout as a mockup and figure out the lengths that way.

Either way, I have all the boards soldered, so now I can get to the mechanical build.



## All 8 Channels Fixed!

**2/8/2019** - I finally managed to get all 8 channels working! Originally, the FPGA could only handle a single channel, and running any more channels would cause it to miss notes and eventually freeze/glitch out. Ultimately, the problem had to do with my baud-rate generator. I simplified the design, which by doing so greatly improved the accuracy of the Serial to Parallel shifter used to decode the MIDI. The original design used a clock rate 16 times faster than the baud and would count 8 "ticks" to get centered in the message. Since that was driven by the clock anyways, I skipped a step and just had it count an equivalent number of clock cycles (800 clock cycles is half the period of a 31250 baud UART message). This completely fixed the decode issue!

Another thing I did was redesign the combinational logic the went on in the rest of the system. The reason was so that it would be easier to convert to a polyphonic setup in the future. Instead of using multiplexers and demultiplexers for controlling signal direction and note on/off control, I have a Data Router module and Channel Registers. Each note can be stored in a register that has an enable and reset control built in. The note and velocity data is put on a common bus and the Data Router sets the specific enable or reset line high to transfer (or clear) the intended register. The reason for doing this is that for polyphony (playing more than one note at a time on a single channel) I will need to assign a note to a single vacant register. By adding a little bit more logic to the data registers, we can ensure that each note gets sent to the first vacant register. You can ensure this by checking the data bus and the contents of the register. If they match, then the note has been added. This logic can be fed into an AND Gate with the clear signal to do the same for a note off command. The white board drawing below shows the basic block diagram for this.

The other reason for implementing the new combinational logic was to ensure that the Pitch and Velocity propagate through the FPGA equally, and stay in sync. Most of the time, the velocity goes straight through the module, but now it has to pass through a bit slower so that it triggers at the same time as the note is being played.







## Multicolor 3D Printed Flags

**2/9/2019** - Something that I did for the original Stepper Synth V1 was that I added "Flags" to the shafts of the motors. The purpose was to highlight the motion of the motors. They were 3D printed on my Original Prusa i3 MK3 and had "JZK" (my initials) embossed into them. I now have the MMU2 (multi-material upgrade V2) installed on my machine, which allows me to print up to 5 colors per layer! Therefore, I redesigned the flags to have the VT (athletic) logo in maroon and orange to make the flags pop out! Also, the athletic logo looks cool and is easy to draw in CAD, unlike the other VT logo...

I also put in a split so that they can fit on the shaft easier with a press-fit, which was the challenge with the old version. Since they are small, a set of 32 only takes about an hour or two to print (which for multi color 3D prints is extremely fast) Essentially I drew in a sketch of the motor shaft and general contour and extruded it 5mm. After that, I used the "Sketch Picture" tool to place an image of the VT logo and traced over it. Then, I did a cut-extrude 0.4mm (about two layers on a 3D print). Finally I used the "convert entities" tool to copy the sketch of the logo in the recess, then extruded it back up again, but I disabled the "Merge Bodies" option. By keeping the extrude body separate, I could export the two as separate STL files and bring them into Slic3r Prusa Edition as a multi-material model. The logo will print face-down, so that the surface is smooth. Also, that surface will often create what is known as "elephant's foot", where the first layer creates a small lip due to it being squished against the print bed. I prefer having this over the print not sticking.

The picture shown might have the wrong colors, as I wasn't going for accuracy here (and I am colorblind) but I think this is close enough for you to get the idea. A great thing about filament is that they write the color on the spool so I can get my colors right!





## Full Test 1

**2/12/2019** - I decided to do a test with all 32 motors connected. The test went great and I can confirm that the system works as intended. The aluminum extrusions came in, but unfortunately the M3 screws I chose for mounting the stepper motors to the acrylic were just barely too long. This means that I have to order some shorter screws to mount the motors to the acrylic. The order should come in on Thursday, so I should be able to assemble on Friday!

Something Bob Lineberry and I discussed was the acoustic properties of my mechanical build. Bob was concerned that the acrylic might dampen the sound, but luckily I planned ahead with this. Most of the vibrations come off the side of the motors, and aluminum is an excellent material to amplify vibrations! It just happens that there are aluminum extrusions between every row of motors that transfers the vibrations to the chassis. I confirmed that the extrusion will work well by using a piece of scrap extrusion I found (left by the RoboGrinders likely). 

I also had one of the channels with the drivers upside down, so I accidentally fried a set of A4988 modules. Luckily, I has some spares and they are really cheap to replace. Nothing else was damaged luckily!





## Prototype Final Assembly

**2/15/2019** - The final assembly of the MIDI Stepper Synth V2 took place today (and a little bit of yesterday). Now that I had replaced the screws, which I found originally too long for the acrylic panels, I could begin the long and tedious process of attaching all 32 stepper motors to the acrylic panel with the 128 M3 screws needed. 

As noted in the last entree, there are aluminum extrusions between every row of the motors, to amplify sound, and because I was concerned about the weight of the stepper motors on the panel. It appears that my suspicions were correct about this, because the weight combined with me likely over-tightening the screws seemed to cause the panel to crack in some of the screw holes. I am not sure if the cracks will continue to spread or if this is a major concern, aside from cosmetic, but if it is, I can easily replace it with a panel of a different material such as Poly-carbonate (Lexan) or PETG, or similar clear material (if possible). Fortunately the way that the synth is built is such that removing the front panel can be done without the motors moving around too much. 

Prior to the mounting of the stepper motors, I screwed the aluminum extrusions together. I had thought I had gotten standard 2020 V-slot, such that I could use standard V-slot/T-slot nuts, but something was wrong with the nuts, or the extrusions, such that I couldn't just slide them in and twist. Instead, I would have to push the nuts in from the end of the extrusions and slide them into place and secure. It was more of a pain, but doable.



Once the panel was attached to the frame, I went through and created a harness for each channel and labeled all the connectors with the label maker. Since there are 32 connectors, it would be easier to get the motors mixed up, so a nice label helps for serviceability in the future if that becomes necessary.



After that, I mounted the 9 power supply bricks using zip-ties. There are two horizontal extrusions just behind the motors that allow for each end of the power supply to be secured. Having the power supplies like this also creates a "layer" that the motors can sit against should the front panel need to be replaced.



Now onto the back panel. All the standoffs were installed on the acrylic. The interface board and FPGA were both mounted to the panel. Because I wanted users to see the PCBs, I had to install the boards upside down. The process for doing this was to plug in the motor cables, then the ribbon cable. I did this for channels 1, 3, 5 and 7 first, because those boards needed the power supply cable routed under the even channels (2, 4, 6 and 8), I plugged in the power supplies, then repeated for channels 2, 4, 6 and 8.  This was then followed by the ribbon cables and channel pairs being zip-tied. With all this wiring, good cable management is a must!



After this, I did a test to make sure that my wiring was good before closing the case up, and the test was successful. I know that if I hadn't done this, Murphy's law would have made sure that it wouldn't work!

Seeing that it worked, I secured the back panel to the frame and secured all the wire harnesses and bundled up all the DC power supply cables. And that concluded the assembly of the MIDI Stepper Synth V2!





Now for the moment of truth. The first test of the fully assembled machine. As a first song, I felt it would only be fitting to play "First Steps/Pointless Machines" by Lena Raine from the video game "Celeste". Poetic, isn't it? Well let's just say that the type of feeling I got from the test was satisfaction, the very type you get from creating something awesome. That's the reason I like to create things and like engineering as a field. 

I will be working with some Music Tech Students to compose some cool music for this machine, as well as professionally record the songs I made for the synth.

One last thing I wanted to think about was that this machine is incredibly heavy (about 40-50 lbs). I think it would be a good idea to get a case for transport of the synth, as I don't want to carry this by the extrusions long distances. Also, that would be just asking for it to be dropped or something break due to stress in an unintended area. It's a musical instrument after all, so it should have a case!

## Begin Final Revision Assembly (2.4)

**2/18/2019** - it seems that the MIDI Stepper Synth V2 is at the point where we can consider it a complete product. After a discussion with Dr. Lineberry, we should start that process of constructing the Stepper Synth that I keep. I will need to test and see how much power that the synth Actually draws so that I can use a single power supply. I can also use parts that won't break in place of the cracked acrylic to ensure that the build is more successful. This would include different 2020 extrusions so that the T-slot nuts actually fit in the extrusion!

We will also be getting a tablet to go with the first Stepper Synth to be used to play music in the amp lab. Something like this should work well. We will also need to get a USB to MIDI adapter to communicate with the synth.

## Better MIDI parsing Software

**2/19/2019** - in preparation for the Stepper Synth becoming a display piece for the Amp lab, I decided to look into software that could play the stepper synth, and not require too much processing power. Also, I was having the issue of certain notes being missed, which I was fairly certain was because of the DAW, not the synth. 

The first thing I tried was using the built-in MIDI out that MuseScore 3 has. This confirmed my suspicions about it being software related, as all the notes were being played perfectly. The only problem with this was that MuseScore doesn't handle pausing very well, as it does not send a MIDI Note Off command to every channel when you press pause.

After some digging, I found a piece of software called "Notation Player 3" which has the single purpose of playing back MIDI files. Testing showed that this program worked perfectly for the job! It also showed me that I had a problem with my MIDI files in MuseScore, as there isn't an option to configure the MIDI channels in Notation. The fix was to open the Mixer window in MuseScore and make sure the MIDI channel numbers were set properly and then re-export the MIDI files.

## Power Supply Considerations and PCB 2.4

**2/24/2019** - Over the past few days, I have been doing some testing for the final revision of the stepper synth. In regard to the power supply, I hooked a single channel up to a power supply and measured the current draw under various notes and full velocity. The most I could get on average was a current draw of 450mA, which is a long shot from the 5A I was giving it. However, there is often a current spike that occurs when the stepper motor starts up, to overcome the inertia that is needed in the motion transient. By setting the power supply to OCP (Over Current Protection), I could see how much the maximum current is approximately. This gave us around 600mA needed. To be safe, I assumed that each channel needed 1A, so the closest power supply was a 12V, 10A supply. Just to be extra safe, I did some research to make sure that the power supply could handle back-EMF that might be generated by the motors. According to the manufacturer, the power supplies have protection (so they won't get damaged) and can handle 10% above their rating before the protection kicks in. They recomended that I have a Zener Diode attached to the motors, which luckily is built into the A4988 IC chips. I believe that the extra head-room in current for this supply should give us a big enough safety margin for the extraneous current spikes. 

I should also note that the A4988 has a built in over-current protection potentiometer that you set depending on the maximum current draw, which would include the motion transient. In short, I should be fine.

On another note, I worked on a new PCB design for the stepper synth, named V2.4. It is mostly the same, with the connectors and revisions to make assembly easier.

One of the most difficult things about the soldering of the boards was the pin headers. The headers have no kink in them, so you had to secure them while soldering otherwise they would fall out when you flipped them over to solder. I had remembered that the Digilent PIC32 dev boards that the students had been using for senior design projects had a 90 degree header that you had to solder in. I had also remembered that when I would have to solder the header in for a student(s), this issue was gone! This was because the pads on the board were in a zig-zag pattern that held the pins in through friction. After doing some digging, I found a way to do this in eagle. Simply offset each pad by 5 mils so that the pads are 10 mils apart on the y axis. The coordinates will be something like this: (0, -5), (100, 5), (200, -5)...

I ended up using the Sparkfun eagle library as a basis for this and modified it to work with my pin headers. 

The only other revision was that I changed the barrel connectors for a 4-pin mini DIN for the 10A power supply and added screw terminals for the motor board power supplies. Everything else, including the board size and mounting scheme remained the same. 

The change in power supply actually had a significant cost offset to the design, as now the whole device, including assembly and case is now the price of what the electronics were (about $800 total now)

(Note that the below 3D renders were done in KiCAD, where I imported the Eagle files and assigned STEP models to the board parts. Eagle is rather terrible at 3D exporting, but KiCAD is awesome at it)









## AMP Lab Display Unit (Tablet Mount)

**2/16/2019** - Added a tablet to the Display Unit. It is a Chuwi Hi8 Tablet, and runs full Windows 10. For $110, I am more than impressed by the performance, as it has a good display and relatively fast performance. I measured the dimensions of the Tablet with my calipers and 3D printed a mounting stand for the Stepper Synth. The holder has 3 Pieces of double-sized tape to cushion the tablet and hold it in place. I installed Notation Player 3 and loaded on the MIDI files. Testing shows that the tablet will work for the job. 

I also put on a wallpaper with instructions on how to use the stepper synth, and changed the account photo to a stepper motor. Now all that is needed is a USB-C hub so that I can charge the tablet and run the USB-MIDI adapter.



## Final Assembly Complete

**3/15/2019** - Assembly of the final MIDI Stepper Synth V2 has been completed. This process took significantly longer than expected, mainly because of a delay in getting the polycarbonate panels cut. (Special thanks to the Robogrinders for helping get the panel cut!) Polycarbonate can be a bit tricky to cut because you cannot use a laser to cut it (it will catch fire if you do) and it has a tendency to melt onto milling bits if you don't use correct feeds and speeds. You need to cut with a slow speed and a fast feed (meaning that the bit should spin slowly and the toolhead should move fast) to prevent this from happening. Once the panels arrived, there were burs and chunks of polycarbonate that needed to be removed. A countersink drill bit along with a sharp xacto knife made quick work of this.

As for the PCB Assembly, the new features added in the 2.4 boards worked flawlessly. The only issue was that I chose the wrong hole size for the 4-position terminal block on the interface board, so I couldn't use that. Instead, I soldered a heavy gauge wire to the terminals on the DIN connector. The wire connected to the 8 pairs of wires that connect to each motor board.

Wire management was made significantly easier by putting twists in wire sets. I did this to all the motor cables by releasing two of the 4 wires (Blue and Red specifically) and putting a twist then re-connecting the dupont pins to their socket. This is something that I saw on all the motors on my Prusa i3 MK3 3D Printer and it eliminates the need for any zipties. I also did this twist to the power cables. I foresee someone talking about this method only being for signaling but I don't see why that would mean that I can't use it elsewhere in the design.

The use of metal corner brackets and true 2020 V-slot extrusions made for a frame that was rock-solid and I could properly tighten the nuts without risk of damaging the bracket or any other part. For the motors, I used an M3 and M5 washer on all the M3 screws so that the pressure was distributed on the panel to lower risk of cracking and I opted to not use any threadlocker and instead simply perform regular checks on the screw tightness. The motors were a rather tight fit so the horizontal extrusions do an excellent job of holding the motors to the panel even without mounting screws. The only hitch on this part was that one of the motors had a bad thread on one of the corners so I could only mount 3 of the 4 points on that one. This shouldn't be a problem aside from cosmetically standing out.

Once all the motors were mounted, I put a twist in each channel to hold the cables together. This meant I only needed a total of 3 zipties per channel; one at the beginning, one to adjust the length, and one at the end. Plugging the cables in was an incredibly easy task because of this, and final cable management required very little effort.

The end result was a very robust machine that weighs less (I don't feel like I am gonna break my back if I lift the thing for two seconds), is more modular and slightly louder. I think at this point I can call this project complete after I update the PCBs to fix the small mistake I made. I will also add a link to the YouTube playlist once I start publishing videos on the subject.











## MIDI Stepper Synth V2 YouTube Playlist

I have started posting YouTube Videos of the MIDI Stepper Synth in action. The songs can be seen [HERE.](https://www.youtube.com/playlist?list=PL4FFrmT3l_b1w0-UKtJ3XjHV_M55FEpmH)

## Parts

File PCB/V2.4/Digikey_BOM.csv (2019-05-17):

Manufacturer Part Number | Manufacturer | Digi-Key Part Number | Customer Reference | Reference Designator | Packaging | Part Status | Quantity | Unit Price | Extended Price | Quantity Available | Mfg Std Lead Time | Description | RoHS Status | Lead Free Status | REACH Status | US Tariff Status
VES120PS12 | XP Power | 1470-3639-ND |  |  | Box | Active | 1 | 62.00000 | $62.00 | 498 | 21 Weeks | EXTERNAL PSU, 120W, LEVEL VI | RoHS Compliant | Lead free | Not Available | Tariff Eligible
PD-40S | CUI Inc. | CP-7240-ND |  |  | Tray | Active | 1 | 2.59000 | $2.59 | 12445 | 14 Weeks | CONN JACK FMALE DIN 4POS SOLDER | RoHS Compliant | Lead free | Not Available | Tariff Eligible
OSTTA020161 | On Shore Technology Inc. | ED2561-ND |  |  | Bulk | Active | 8 | 0.69000 | $5.52 | 16887 | 12 Weeks | TERM BLK 2POS SIDE ENTRY 5MM PCB | RoHS Compliant | Lead free | REACH Unaffected | Tariff Applied
OSTTA040161 | On Shore Technology Inc. | ED2563-ND |  |  | Bulk | Active | 1 | 1.05000 | $1.05 | 976 | 12 Weeks | TERM BLK 4POS SIDE ENTRY 5MM PCB | RoHS Compliant | Lead free | REACH Unaffected | Tariff Applied
61300411121 | Wurth Electronics Inc. | 732-5317-ND |  |  | Bag | Active | 32 | 0.12720 | $4.07 | 16252 | 14 Weeks | CONN HEADER VERT 4POS 2.54MM | RoHS Compliant | Lead free | REACH Unaffected
PPTC081LFBN-RC | Sullins Connector Solutions | S7006-ND |  |  | Tray | Active | 64 | 0.60800 | $38.91 | 21240 | 5 Weeks | CONN HDR 8POS 0.1 TIN PCB | RoHS Compliant | Lead free | REACH Unaffected
0ZCF0100AF2A | Bel Fuse Inc. | 507-2070-1-ND |  |  | Cut Tape (CT) | Active | 32 | 0.49100 | $15.71 | 9184 | 18 Weeks | PTC RESET FUSE 60V 1A 2920 | RoHS Compliant | Lead free | REACH Unaffected
UHE2A470MPD1TD | Nichicon | 493-14555-1-ND |  |  | Cut Tape (CT) | Active | 36 | 0.36000 | $12.96 | 50826 | 16 Weeks | CAP ALUM 47UF 20% 100V RADIAL | RoHS Compliant | Lead free | REACH Unaffected
M20-9760442 | Harwin Inc. | 952-3276-ND |  |  | Bulk | Active | 16 | 0.31900 | $5.10 | 3637 | 10 Weeks | CONN HEADER VERT 8POS 2.54MM | RoHS Compliant | Lead free | REACH Unaffected
SDS-50J | CUI Inc. | CP-2350-ND |  |  | Tray | Active | 1 | 1.96000 | $1.96 | 24579 | 14 Weeks | CONN RCPT FMALE DIN 5POS SOLDER | RoHS Compliant | Lead free | Not Available | Tariff Applied
A 08-LC-TT | Assmann WSW Components | AE9986-ND |  |  | Tube | Active | 1 | 0.18000 | $0.18 | 100334 | 20 Weeks | CONN IC DIP SOCKET 8POS TIN | RoHS Compliant | Lead free | REACH Unaffected | Tariff Eligible
1N914 | ON Semiconductor | 1N914FS-ND |  |  | Bulk | Active | 1 | 0.10000 | $0.10 | 50588 | 17 Weeks | DIODE GEN PURP 100V 200MA DO35 | RoHS Compliant | Lead free | REACH Unaffected | Tariff Applied
61304021121 | Wurth Electronics Inc. | 732-5310-ND |  |  | Bag | Active | 1 | 1.89000 | $1.89 | 924 | 14 Weeks | CONN HEADER VERT 40POS 2.54MM | RoHS Compliant | Lead free | REACH Unaffected
20SVPF120M | Panasonic Electronic Components | P16498CT-ND |  |  | Cut Tape (CT) | Active | 1 | 1.29000 | $1.29 | 34887 | 9 Weeks | CAP ALUM POLY 120UF 20% 20V SMD | RoHS Compliant | Lead free | Not Available
UUD1A471MNL1GS | Nichicon | 493-2252-1-ND |  |  | Cut Tape (CT) | Active | 1 | 0.68000 | $0.68 | 34069 | 18 Weeks | CAP ALUM 470UF 20% 10V SMD | RoHS Compliant | Lead free | REACH Unaffected
B540C-13-F | Diodes Incorporated | B540C-FDICT-ND |  |  | Cut Tape (CT) | Active | 1 | 0.50000 | $0.50 | 259459 | 13 Weeks | DIODE SCHOTTKY 40V 5A SMC | RoHS Compliant | Contains lead | REACH Unaffected
PM2110-101K-RC | Bourns Inc. | M8767-ND |  |  | Bulk | Active | 1 | 2.96000 | $2.96 | 2757 | 20 Weeks | FIXED IND 100UH 5.4A 32 MOHM SMD | RoHS Compliant | Lead free | REACH Unaffected
LM2576SX-5.0/NOPB | Texas Instruments | LM2576SX-5.0/NOPBCT-ND |  |  | Cut Tape (CT) | Active | 1 | 2.86000 | $2.86 | 41842 | 16 Weeks | IC REG BUCK 5V 3A TO263-5 | RoHS Compliant | Contains lead | REACH Unaffected
1988 | Adafruit Industries LLC | 1528-2235-ND |  |  | Bulk | Active | 1 | 2.95000 | $2.95 | 348 | 12 Weeks | GPIO RIBBON CABLE FOR RASPBERRY | Not Available | Not Available | Not Available | Tariff Eligible
71600-008LF | Amphenol ICC (FCI) | 609-3568-ND |  |  | Tube | Active | 16 | 0.87000 | $13.92 | 6728 | 8 Weeks | CONN RCPT 8POS IDC 28-30AWG GOLD | RoHS Compliant | Lead free | Not Available
28L0138-50R-10 | Laird-Signal Integrity Products | 240-2512-1-ND |  |  | Cut Tape (CT) | Active | 10 | 0.07700 | $0.77 | 44108 | 8 Weeks | FERRITE BEAD 153 OHM AXIAL 1LN | RoHS Compliant | Lead free | REACH Unaffected | Tariff Applied
CFM14JT220R | Stackpole Electronics Inc | S220QCT-ND |  |  | Cut Tape (CT) | Active | 2 | 0.10000 | $0.20 | 37986 | 15 Weeks | RES 220 OHM 1/4W 5% CF MINI | RoHS Compliant | Lead free | REACH Unaffected | Tariff Applied
CFM14JT4K70 | Stackpole Electronics Inc | S4.7KQCT-ND |  |  | Cut Tape (CT) | Active | 1 | 0.10000 | $0.10 | 65820 | 15 Weeks | RES 4.7K OHM 1/4W 5% CF MINI | RoHS Compliant | Lead free | REACH Unaffected | Tariff Applied
3801/04 | 3M | 3M156838-10-ND |  |  | Bulk | Active | 1 | 3.79000 | $3.79 | 9 | Not Available | CBL RIBN 4COND 0.050 GRAY 10' | RoHS Compliant | Lead free | Not Available
6N138 | Lite-On Inc. | 160-1795-ND |  |  | Tube | Active | 1 | 0.81000 | $0.81 | 4836 | 10 Weeks | OPTOISO 5KV DARL W/BASE 8DIP | RoHS Compliant | Lead free | Not Available

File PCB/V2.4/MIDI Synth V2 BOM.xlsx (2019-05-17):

Qty | Board | Part No. | Name | Package | Ordering Info | Price ea | Total Price | TOTAL: | $794.03
32 | Driver | U1-U4 | A4988 Breakout Module | N/A | B01FFGAKK8 (http://a.co/d/6b15mfi) | $1.78 | $56.83
32 | Driver | SV1-4 | 4x1 Male Header | Header | 732-5317-ND (https://www.digikey.com/short/j1r95w) | $0.13 | $4.07
64 | Driver | N/A | 8x1 Female Header | Header | S7006-ND (https://www.digikey.com/short/j1r9qq) | $0.61 | $38.91
32 | Driver | F1-F4 | PTC Resetable Fuse 60V 1A | SMD 2920 | 507-2070-1-ND (https://www.digikey.com/short/pch2dd) | $0.48 | $15.23
32 | Driver | C1-C4 | 47uF electrolytic cap | THT | 493-14555-1-ND (https://www.digikey.com/short/pchrdr) | $0.38 | $12.10
16 | Both | SV5, SV2-9 | 2x4 Male Header | Header | 952-3276-ND (https://www.digikey.com/short/p7mp47) | $0.32 | $5.10
1 | Interface | U3 | MIDI Jack | 5 DIN | CP-2350-ND (https://www.digikey.com/short/pch9p7) | $1.96 | $1.96
1 | Interface | U2 | 6N138 Optoisolator IC | DIP8 | 160-1795-ND (https://www.digikey.com/short/pch9pf) | $0.81 | $0.81
1 | Interface | U2 | DIP8 Socket | DIP8 | AE9986-ND (https://www.digikey.com/short/pch9mn) | $0.18 | $0.18
1 | Interface | D1 | 1N914 Diode | DO-35 THT | 1N914FS-ND (https://www.digikey.com/short/pch9zj) | $0.10 | $0.10
2 | Interface | R1, R2 | 220 ohm resistor | THT | S220QCT-ND (https://www.digikey.com/short/ppbfp4) | $0.10 | $0.20
1 | Interface | R3 | 4.7k resistor | THT | S4.7KQCT-ND (https://www.digikey.com/short/ppbfp0) | $0.10 | $0.10
1 | Interface | P1 | 20x2 Male Header | Header | 732-5310-ND (https://www.digikey.com/short/p7m2t8) | $1.89 | $1.89
1 | Interface | C1 | 120uF electrolytic Cap | SMD | P16498CT-ND (https://www.digikey.com/short/p7mjtn) | $1.36 | $1.36
1 | Interface | C2 | 470uF electrolytic Cap | SMD | 493-2252-1-ND (https://www.digikey.com/short/p7mjtc) | $0.68 | $0.68
1 | Interface | D2 | B540C Schottky Diode | SMD SMC | B540C-FDICT-ND (https://www.digikey.com/short/p7mjcv) | $0.55 | $0.55
1 | Interface | L1 | 100uH Toriodal Inductor | SMD | M8767-ND (https://www.digikey.com/short/p7mjcz) | $2.96 | $2.96
1 | Interface | U1 | LM2576 5V Buck Regulator | TO-263-5 | LM2576SX-5.0/NOPBCT-ND (https://www.digikey.com/short/p7m81t) | $2.86 | $2.86
1 | Interface | N/A | 40 pin GPIO Ribbon Cable | IDC | 1528-2235-ND (https://www.digikey.com/short/pqqj4f) | $2.95 | $2.95
16 | Both | N/A | 2x4 IDC Connector | IDC | 609-3568-ND (https://www.digikey.com/short/pq3194) | $0.84 | $13.39
1 | Interface | N/A | DE0-nano FPGA | N/A | Adafruit, (Already Have!) (https://www.adafruit.com/product/451) | $99.00 | $99.00
10 | Driver | N/A | Stepper Motor Driver PCB V2.4 | N/A | JLCPCB 95x60mm size (leave everything else default!) | $5.00 | $5.00
10 | Interface | N/A | Interface PCB V2.4 | N/A | JLCPCB, 90x90mm size (leave everything else default!) | $5.00 | $5.00
32 | Driver | N/A | NEMA 17 Stepper Motor | N/A | SteppersOnline, 17HS15-1504S1 (https://www.omc-stepperonline.com/17hs15-1504s1.html#.XDeEUXQHGLE.link) | $6.43 | $205.76
0 | Both | N/A | Ribbon Cable for IDC connectors | Ribbon Cable | 3M156838-10-ND (https://www.digikey.com/short/ppbfmt) | $3.79 | $0.00
8 | Driver | R1 | Ferrite Bead | THT | 240-2512-1-ND (https://www.digikey.com/short/p7mmtn) | $0.10 | $0.80
8 | Driver | CN6 | 2 Position Screw Terminal | THT | ED2561-ND (https://www.digikey.com/short/pq31n1) | $0.69 | $5.52
1 | Interface | N/A | 4 Position Screw Terminal | THT | ED2563-ND (https://www.digikey.com/short/pq3105) | $1.05 | $1.05
1 | Both | N/A | 12V 10A Power Supply | N/A | 1470-3639-ND (https://www.digikey.com/short/pq31v0) | $62.00 | $62.00
1 | Interface | J1 | 4 Pin MINI DIN | THT | CP-7240-ND (https://www.digikey.com/short/pqqccj) | $2.59 | $2.59
 |  |  |  |  |  |  | $0.00
2 | Mechanical | N/A | M3 x 8 Screws | Mechanical | B07C6DKT3H (https://www.amazon.com/WLine-Stainless-Button-Socket-Including/dp/B07C6DKT3H?s=hi) | $6.99 | $13.98
2 | Mechanical | N/A | M3 Standoff 40mm | Mechanical | B01LOIKEWU (https://www.amazon.com/dp/B01LOIKEWU/ref=sspa_dk_detail_7?psc=1&pd_rd_i=B01LOIKEWU) | $10.99 | $21.98
4 | Mechanical | N/A | 2020 V-Slot (1500mm each) | Mechanical | B00YCOQO5A (https://www.amazon.com/V-Slot-Linear-Rail-1500mm-Length/dp/B00YCOQO5A) | $15.99 | $63.96
1 | Mechanical | N/A | M5 T-Slot Nut | Mechanical | B072MDW1YY (https://www.amazon.com/IZTOSS-100PCS-Assembly-Aluminum-Profile/dp/B072MDW1YY?s=Home+Improvement) | $13.99 | $13.99
2 | Mechanical | N/A | M5 x 8mm Pan Head Screw | Mechanical | B07DRHN4V4 (https://www.amazon.com/iExcell-Socket-Button-Easy-use-Storage/dp/B07DRHN4V4?s=hi) | $9.99 | $19.98
1 | Mechanical | N/A | M3 washers | Mechanical | B018TG8D6E (https://www.amazon.com/gp/product/B018TG8D6E/ref=ppx_yo_dt_b_asin_title_o04_s00?ie=UTF8&psc=1) | $5.19 | $5.19
 |  |  |  |  |  |  | $0.00
1 | Case | N/A | Travel Case for Stepper Synth | Case | #VALUE! (https://www.amazon.com/Seahorse-920F-Protective-Wheeled-Case/dp/B00153U9NE) | $105.99 | $105.99
 |  |  |  |  |  |  | $0.00
 |  |  |  |  |  |  | $0.00
 |  |  |  |  |  |  | $0.00
 |  |  |  |  |  |  | $0.00
 |  |  |  |  |  |  | $0.00
 |  |  |  |  |  |  | $0.00
 |  |  |  |  |  |  | $0.00
 |  |  |  |  |  |  | $0.00
 |  |  |  |  |  |  | $0.00
 |  |  |  |  |  |  | $0.00
 |  |  |  |  |  |  | $0.00
 |  |  |  |  |  |  | $0.00
 |  |  |  |  |  |  | $0.00
 |  |  |  |  |  |  | $0.00
 |  |  |  |  |  |  | $0.00

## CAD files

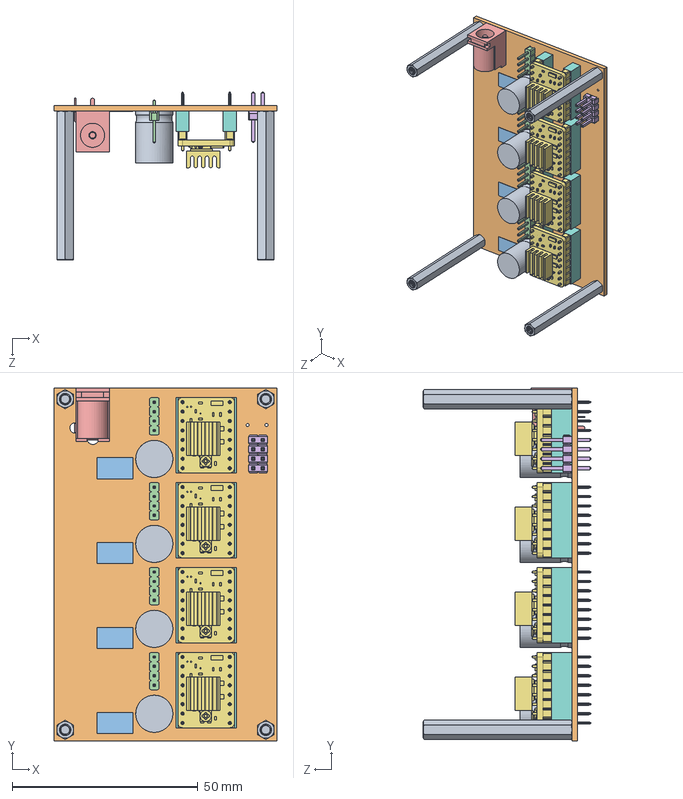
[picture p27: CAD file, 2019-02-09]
SolidWorks/MotorAndStandoff.SLDASM
60.0 x 95.0 x 45.1 mm
95947A500_ALUM FEM THRDED HEX STANDOFF x 4
Board
PTC2920_0ZCF x 4
1x4 Male Header x 4
Barrel Jack
2x4 Male Header
A4988 Board x 4
1x8 Female Header x 8
47uF Cap x 4

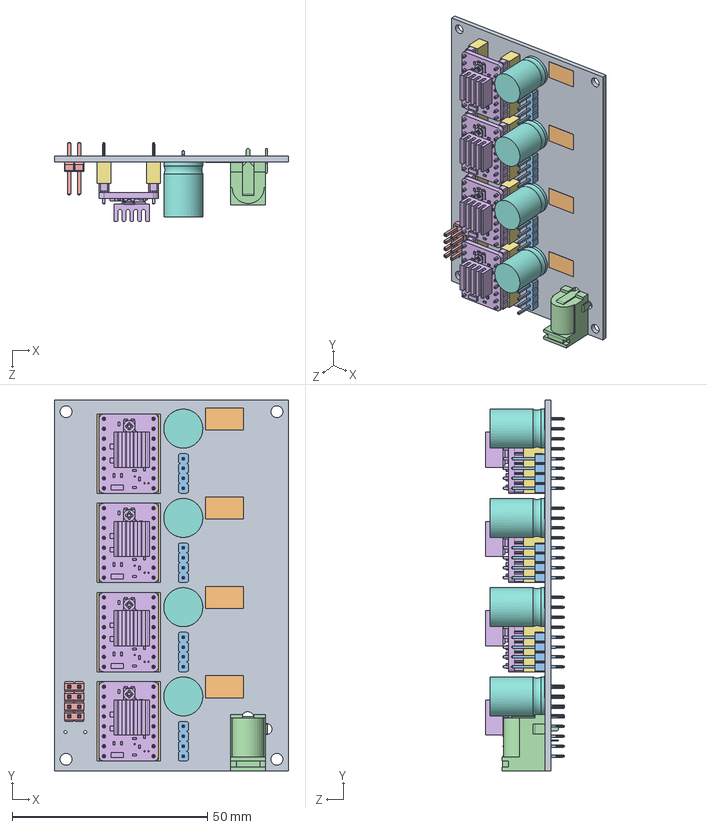
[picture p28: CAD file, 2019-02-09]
SolidWorks/StepperSynth2.3_Motor.SLDASM
60.0 x 95.0 x 20.3 mm
Board
PTC2920_0ZCF x 4
1x4 Male Header x 4
Barrel Jack
2x4 Male Header
A4988 Board x 4
1x8 Female Header x 8
47uF Cap x 4

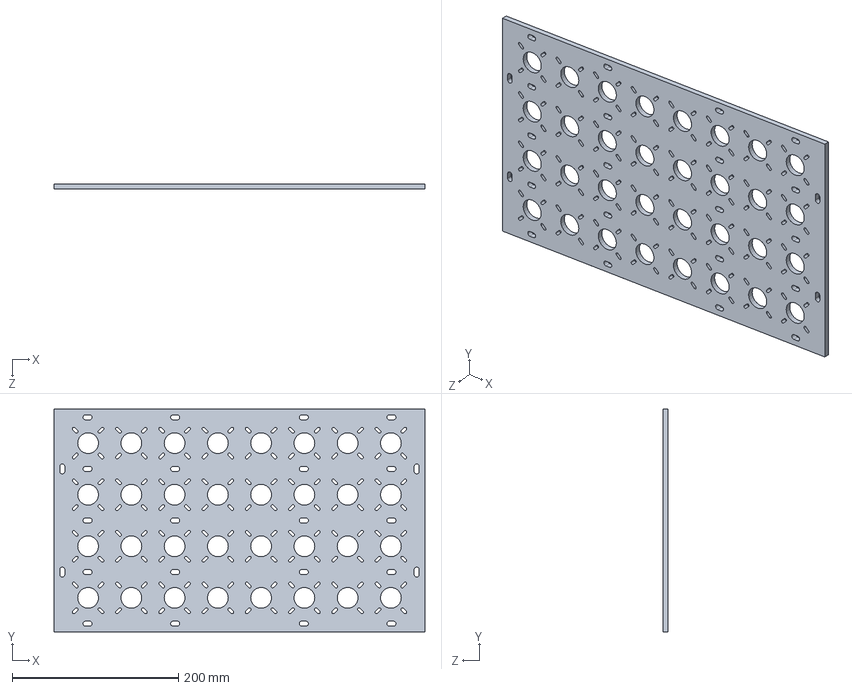
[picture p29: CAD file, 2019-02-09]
SolidWorks/Front Acrylic Panel.SLDPRT
446.0 x 268.0 x 6.35 mm

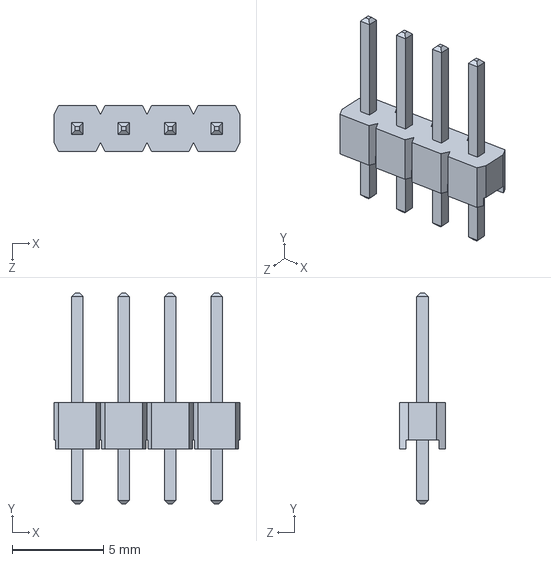
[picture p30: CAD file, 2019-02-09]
SolidWorks/1x4 Male Header.SLDPRT
10.2 x 11.5 x 2.54 mm

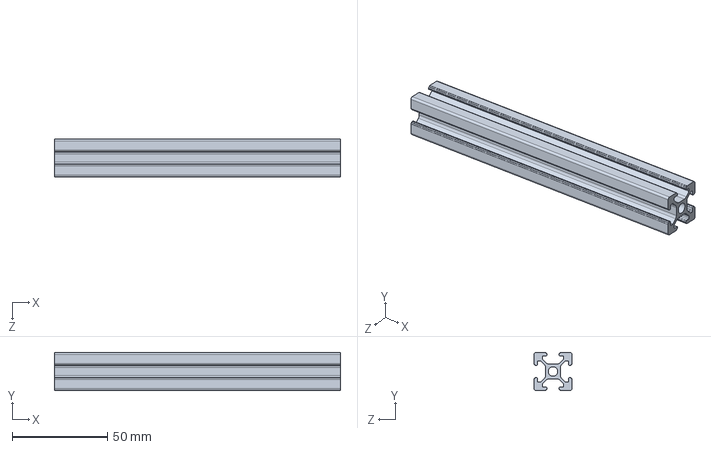
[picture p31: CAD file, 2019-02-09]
SolidWorks/Y Extrusion.SLDPRT
150.0 x 20.0 x 20.0 mm

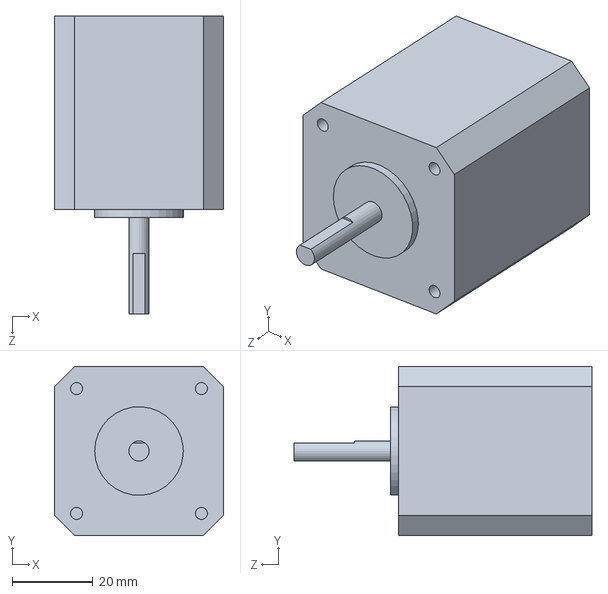
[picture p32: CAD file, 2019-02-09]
SolidWorks/NEMA17.SLDPRT
42.0 x 42.0 x 74.0 mm

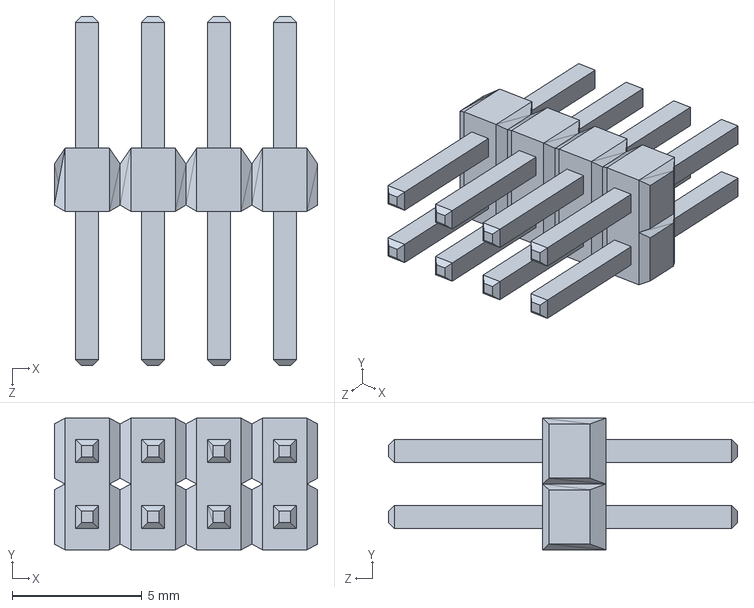
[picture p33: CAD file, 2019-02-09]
SolidWorks/2x4 Male Header.SLDPRT
10.2 x 5.08 x 13.5 mm

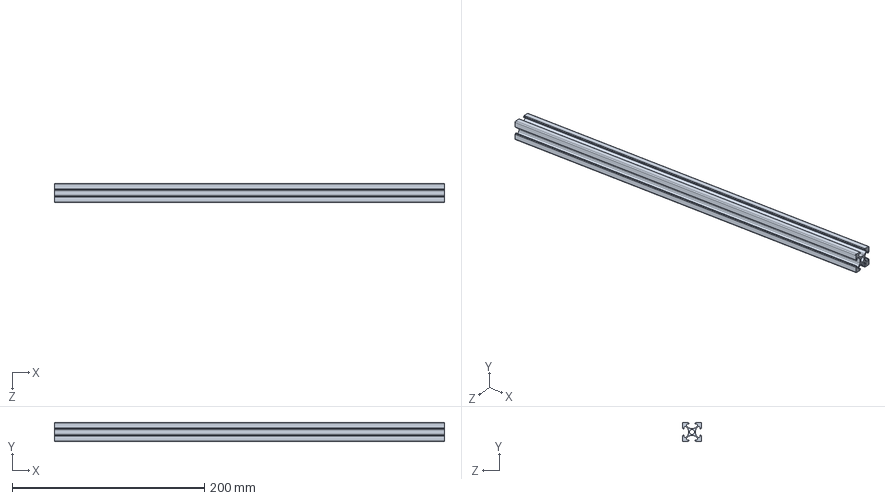
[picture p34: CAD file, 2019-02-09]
SolidWorks/X Extrusion.SLDPRT
406.0 x 20.0 x 20.0 mm

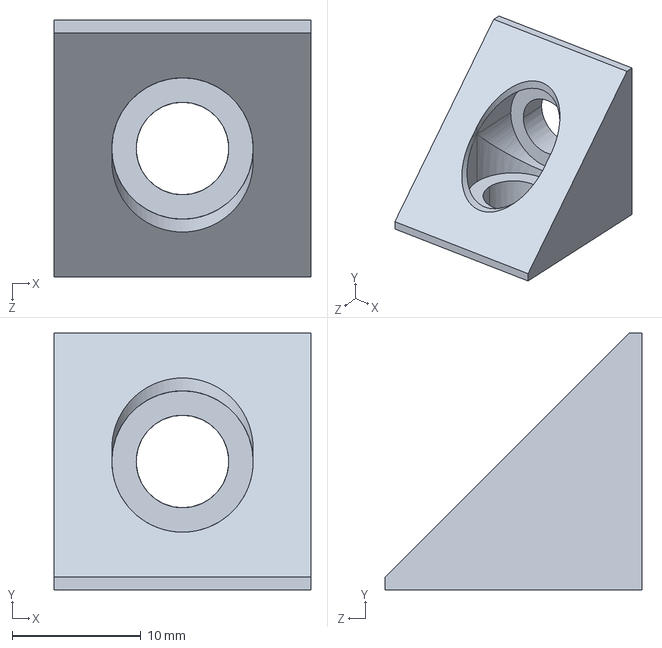
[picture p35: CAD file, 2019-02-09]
SolidWorks/Black Angle Corner Connector.SLDPRT
20.0 x 20.0 x 20.0 mm

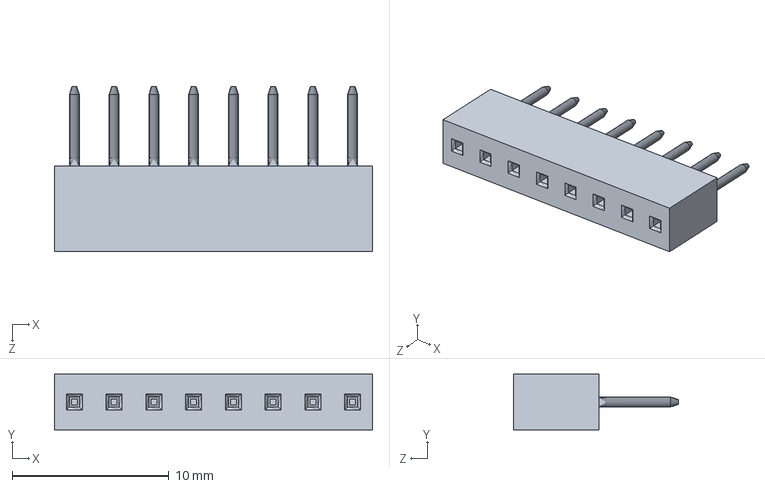
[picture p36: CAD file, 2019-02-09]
SolidWorks/1x8 Female Header.SLDPRT
20.3 x 3.56 x 10.5 mm

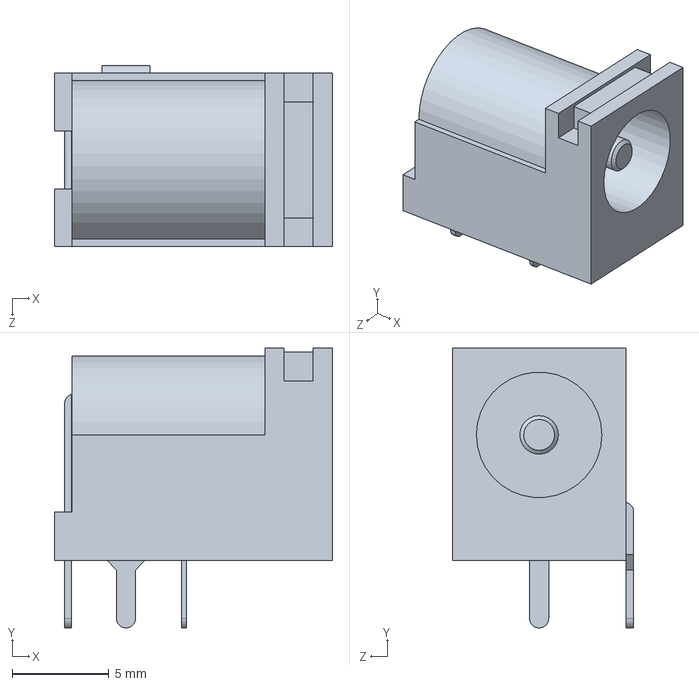
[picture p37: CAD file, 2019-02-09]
SolidWorks/Barrel Jack.sldprt
14.4 x 14.5 x 9.40 mm

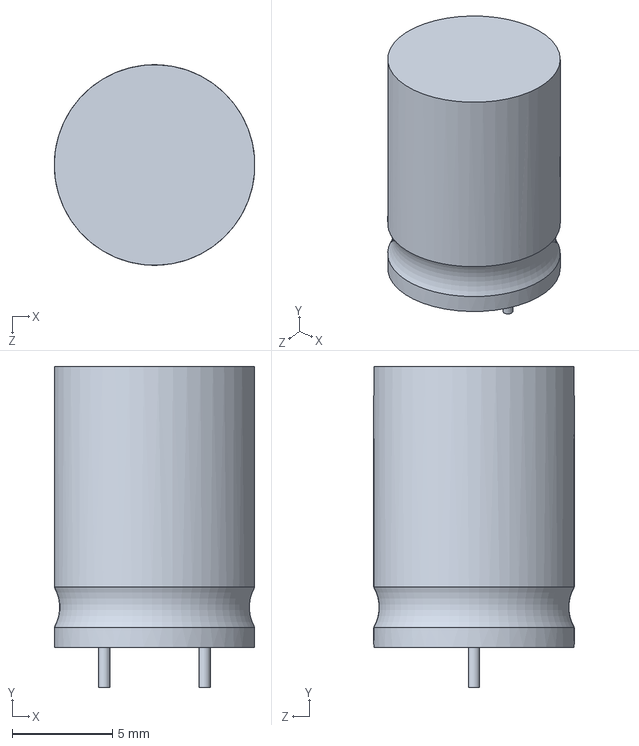
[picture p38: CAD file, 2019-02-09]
SolidWorks/47uF Cap.SLDPRT
9.99 x 16.0 x 10.00 mm

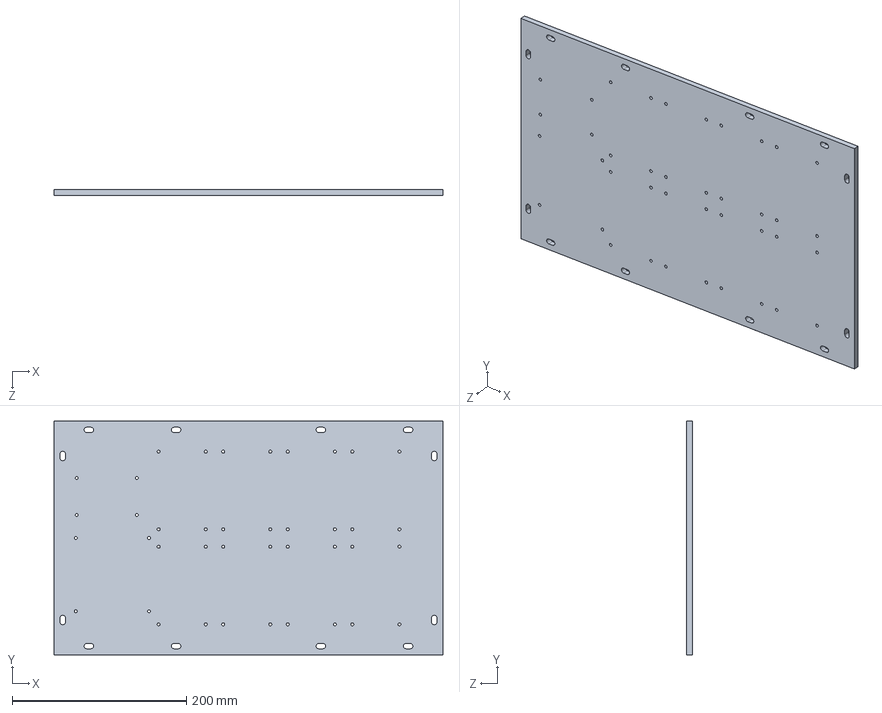
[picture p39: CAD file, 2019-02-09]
SolidWorks/Back Acrylic Panel.SLDPRT
446.0 x 268.0 x 6.35 mm

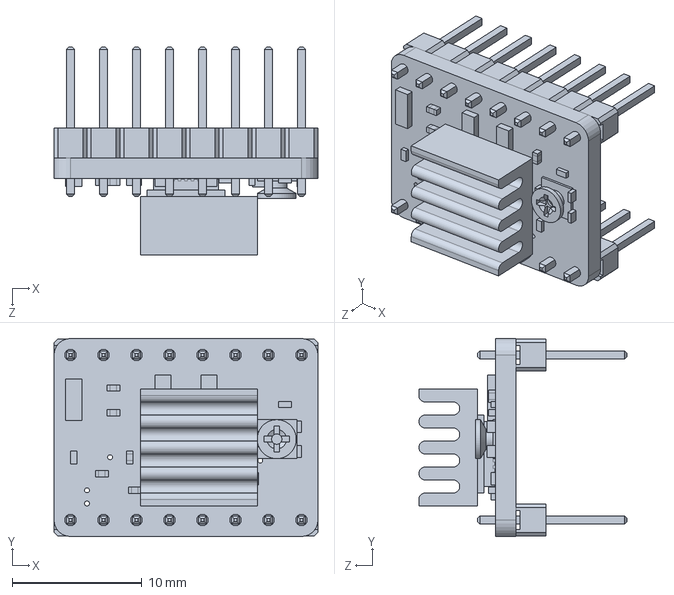
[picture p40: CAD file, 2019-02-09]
SolidWorks/A4988 Board.SLDPRT
20.3 x 15.2 x 16.0 mm

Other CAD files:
SolidWorks/PCB Component.sldasm
SolidWorks/Board.sldprt
SolidWorks/PTC2920_0ZCF.sldprt
SolidWorks/Interface PCB.SLDPRT
SolidWorks/95947A500_ALUM FEM THRDED HEX STANDOFF.SLDPRT
SolidWorks/Z Extrusion.SLDPRT

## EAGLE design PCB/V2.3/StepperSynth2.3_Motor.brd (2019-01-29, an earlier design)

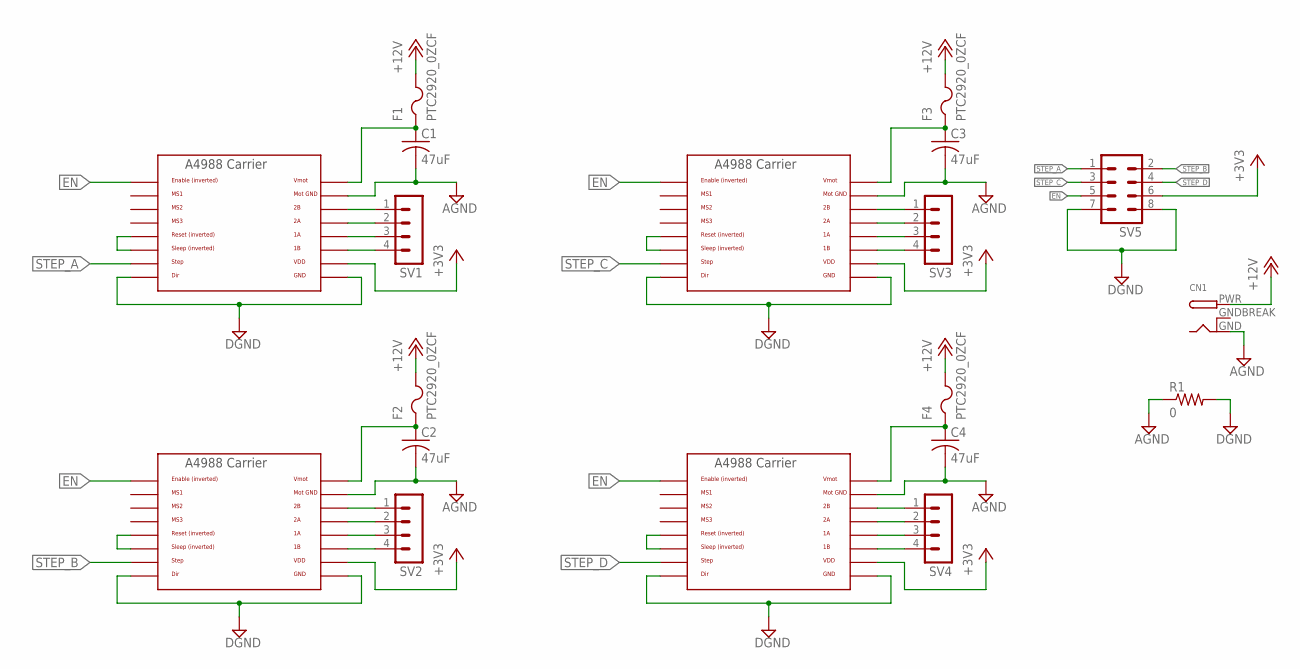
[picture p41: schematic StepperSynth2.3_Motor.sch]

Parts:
C1, C2, C3, C4: 47uF; E5-10
CN1: DCBARRELPTH; DCJACK_2MM_PTH
F1, F2, F3, F4: PTC2920_0ZCF; 0ZCF
R1: 0; 0204/5
SV1, SV2, SV3, SV4: MA04-1
SV5: MA04-2
U$1, U$2, U$3, U$4: A4988BREAKOUT

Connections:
+3V3: SV5.6, U$1.VDD, U$2.VDD, U$3.VDD, U$4.VDD
+12V: CN1.PWR, F1.2, F2.2, F3.2, F4.2
AGND: C1.-, C2.-, C3.-, C4.-, CN1.GND, R1.1, U$1.MOTGND, U$2.MOTGND, U$3.MOTGND, U$4.MOTGND
DGND: R1.2, SV5.7, SV5.8, U$1.DIR, U$1.GND, U$2.DIR, U$2.GND, U$3.DIR, U$3.GND, U$4.DIR, U$4.GND
EN: SV5.5, U$1.EN, U$2.EN, U$3.EN, U$4.EN
GNDBREAK: CN1.GNDBREAK
unnamed: SV1.1, U$1.2B
unnamed: SV1.2, U$1.2A
unnamed: SV1.3, U$1.1A
unnamed: SV1.4, U$1.1B
unnamed: U$1.RST, U$1.SLP (SLEEP)
unnamed: C1.+, F1.1, U$1.VMOT
unnamed: SV2.1, U$2.2B
unnamed: SV2.2, U$2.2A
unnamed: SV2.3, U$2.1A
unnamed: SV2.4, U$2.1B
unnamed: U$2.RST, U$2.SLP (SLEEP)
unnamed: C2.+, F2.1, U$2.VMOT
unnamed: SV3.1, U$3.2B
unnamed: SV3.2, U$3.2A
unnamed: SV3.3, U$3.1A
unnamed: SV3.4, U$3.1B
unnamed: U$3.RST, U$3.SLP (SLEEP)
unnamed: C3.+, F3.1, U$3.VMOT
unnamed: SV4.1, U$4.2B
unnamed: SV4.2, U$4.2A
unnamed: SV4.3, U$4.1A
unnamed: SV4.4, U$4.1B
unnamed: U$4.RST, U$4.SLP (SLEEP)
unnamed: C4.+, F4.1, U$4.VMOT
STEP_A: SV5.1, U$1.STEP
STEP_B: SV5.2, U$2.STEP
STEP_C: SV5.3, U$3.STEP
STEP_D: SV5.4, U$4.STEP

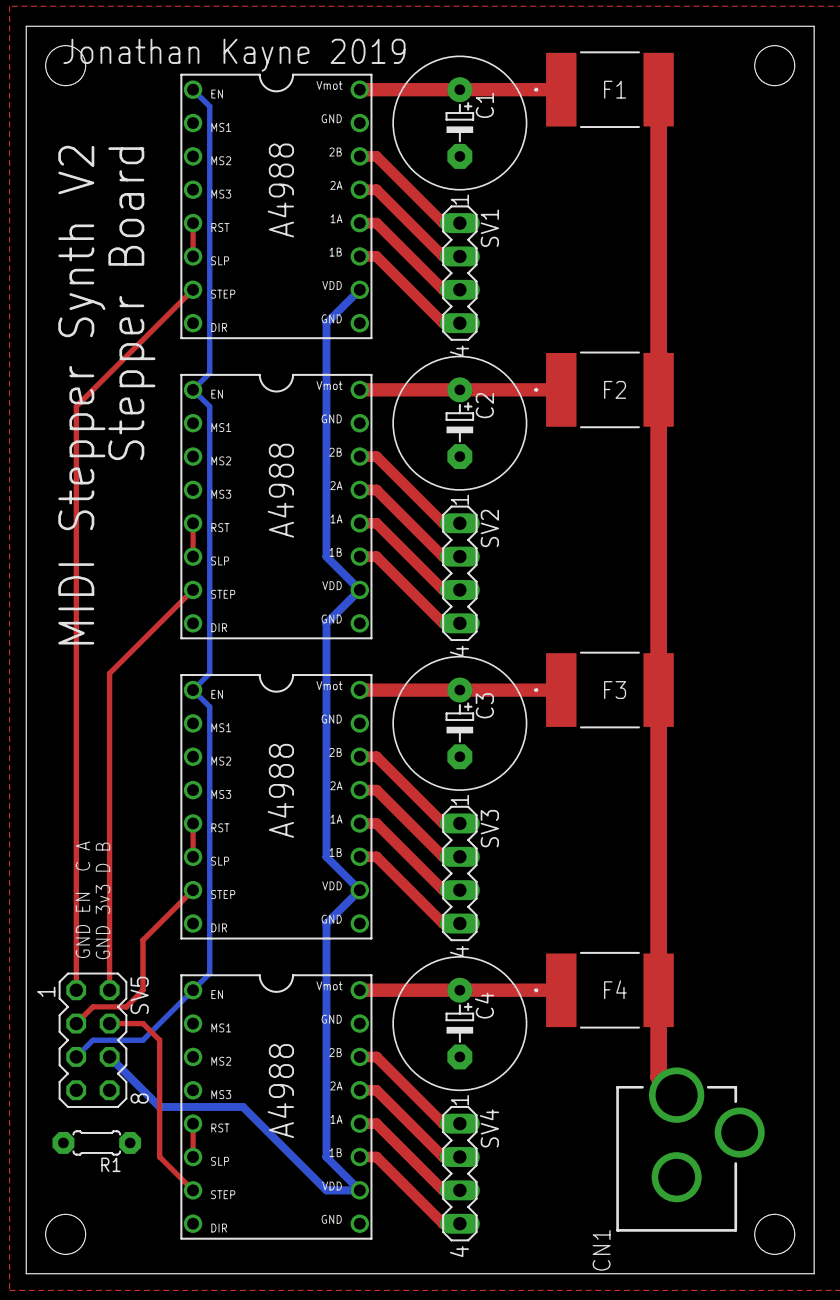
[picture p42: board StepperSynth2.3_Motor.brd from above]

Board: 2 copper layers, 60.0 x 95.0 mm, 19 parts (0 on the bottom side), 33 nets.

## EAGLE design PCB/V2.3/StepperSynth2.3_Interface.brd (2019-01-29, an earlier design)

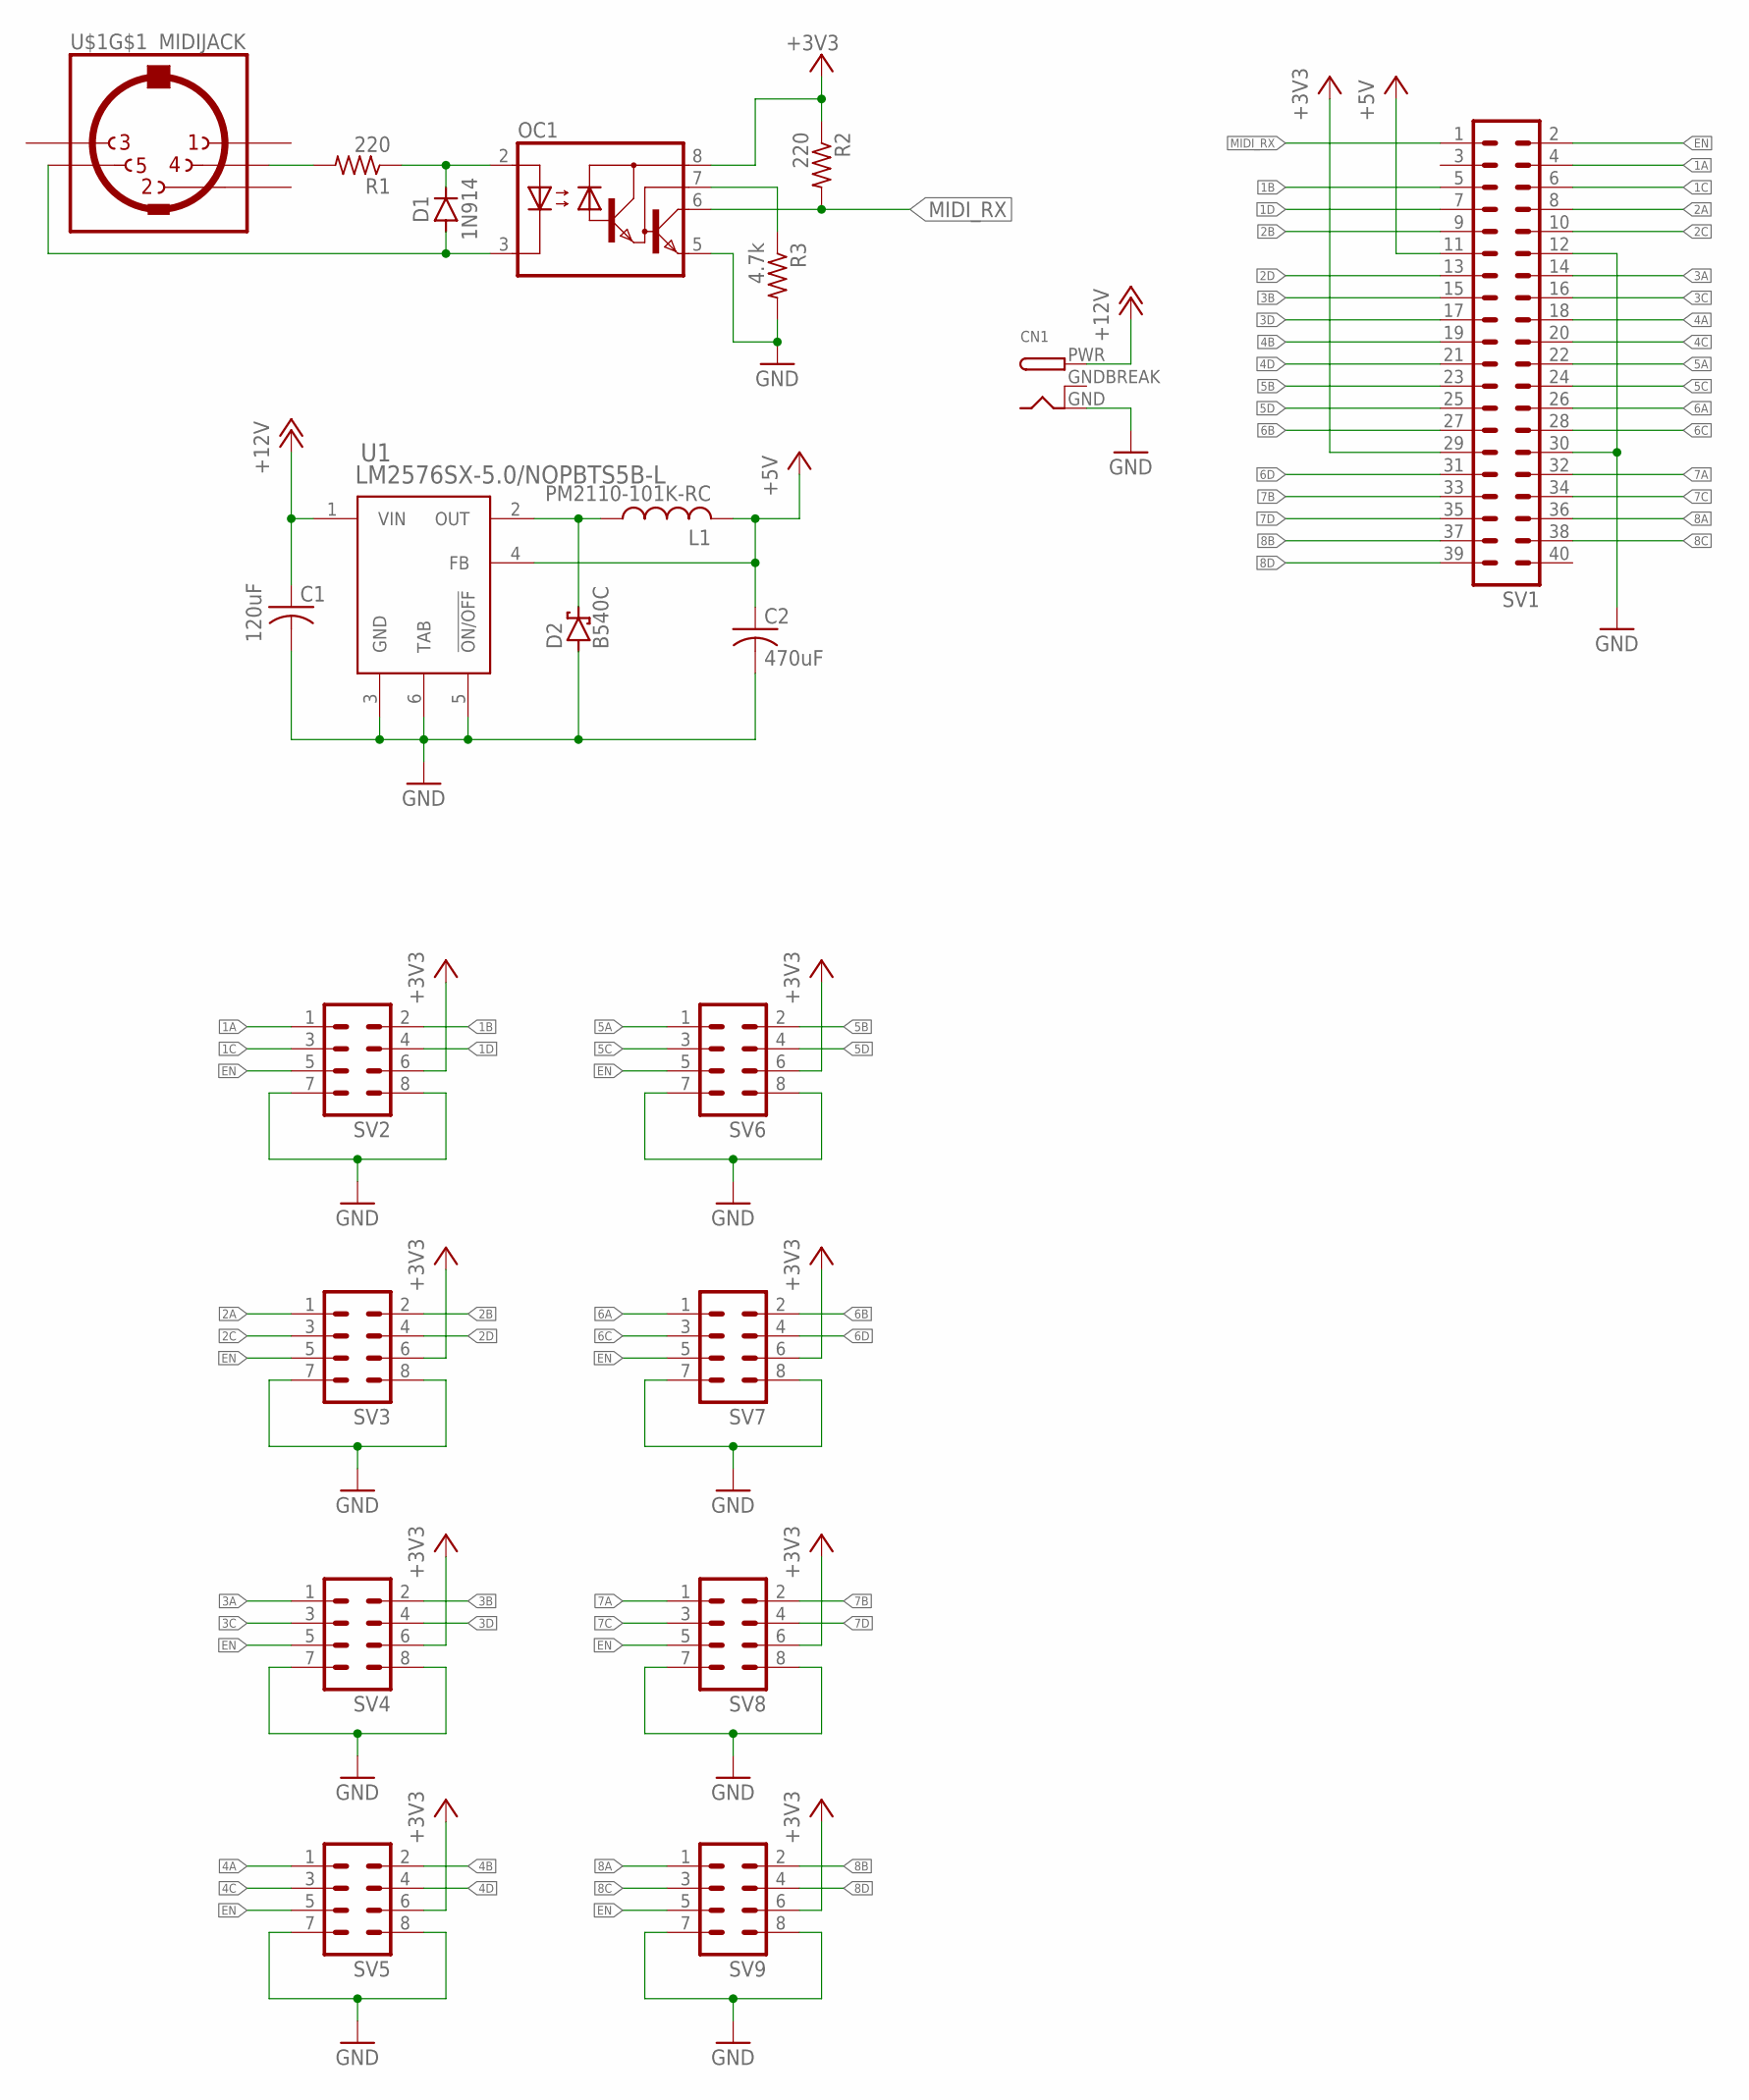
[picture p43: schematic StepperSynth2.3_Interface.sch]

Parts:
C1: 120uF; PCAP_SVP_C6-L
C2: 470uF; U2-P-L
CN1: DCBARRELPTH; DCJACK_2MM_PTH
D1: 1N914; DO35-7
D2: B540C; SMC
L1: PM2110-101K-RC; IND_PM2110
OC1: 6N138; DIL08
R1, R2: 220; 0204/5
R3: 4.7k; 0204/5
SV1: MA20-2
SV2, SV3, SV4, SV5, SV6, SV7, SV8, SV9: MA04-2
U1: LM2576SX-5.0/NOPBTS5B-L; TS5B-L
U$1: MIDIJACK; CP-2350

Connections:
1A: SV1.4, SV2.1
1B: SV1.5, SV2.2
1C: SV1.6, SV2.3
1D: SV1.7, SV2.4
2A: SV1.8, SV3.1
2B: SV1.9, SV3.2
2C: SV1.10, SV3.3
2D: SV1.13, SV3.4
3A: SV1.14, SV4.1
3B: SV1.15, SV4.2
3C: SV1.16, SV4.3
3D: SV1.17, SV4.4
4A: SV1.18, SV5.1
4B: SV1.19, SV5.2
4C: SV1.20, SV5.3
4D: SV1.21, SV5.4
5A: SV1.22, SV6.1
5B: SV1.23, SV6.2
5C: SV1.24, SV6.3
5D: SV1.25, SV6.4
6A: SV1.26, SV7.1
6B: SV1.27, SV7.2
6C: SV1.28, SV7.3
6D: SV1.31, SV7.4
7A: SV1.32, SV8.1
7B: SV1.33, SV8.2
7C: SV1.34, SV8.3
7D: SV1.35, SV8.4
8A: SV1.36, SV9.1
8B: SV1.37, SV9.2
8C: SV1.38, SV9.3
8D: SV1.39, SV9.4
+3V3: OC1.8 (VCC), R2.1, SV1.29, SV2.6, SV3.6, SV4.6, SV5.6, SV6.6, SV7.6, SV8.6, SV9.6
+5V: C2.1 (+), L1.2, SV1.11, U1.4 (FB)
+12V: C1.1 (+), CN1.PWR, U1.1 (VIN)
EN: SV1.2, SV2.5, SV3.5, SV4.5, SV5.5, SV6.5, SV7.5, SV8.5, SV9.5
GND: C1.2 (-), C2.2 (-), CN1.GND, D2.A, OC1.5 (GND), R3.2, SV1.12, SV1.30, SV2.7, SV2.8, SV3.7, SV3.8, SV4.7, SV4.8, SV5.7, SV5.8, SV6.7, SV6.8, SV7.7, SV7.8, SV8.7, SV8.8, SV9.7, SV9.8, U1.3 (GND), U1.5 (!ON/OFF), U1.6 (TAB)
GNDBREAK: CN1.GNDBREAK
MIDI_RX: OC1.6 (VO), R2.2, SV1.1
unnamed: R1.2, U$1.4
unnamed: D1.C, OC1.2 (A), R1.1
unnamed: D1.A, OC1.3 (C), U$1.5
unnamed: OC1.7 (VB), R3.1
unnamed: D2.C, L1.1, U1.2 (OUT)

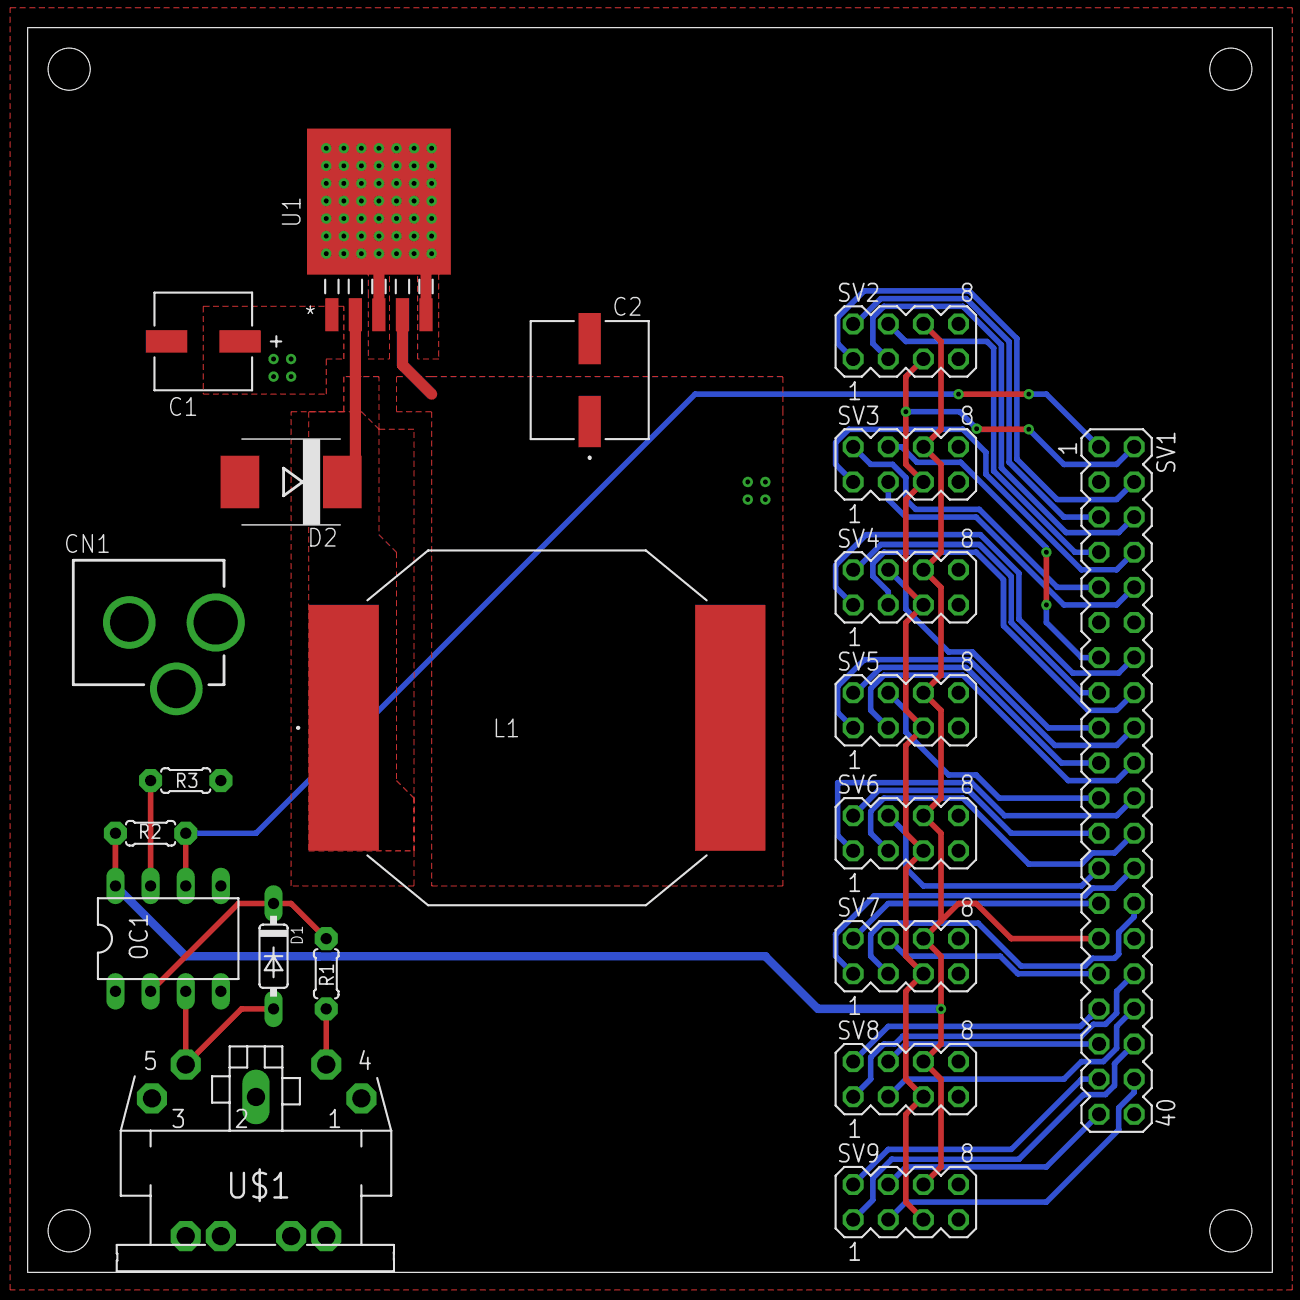
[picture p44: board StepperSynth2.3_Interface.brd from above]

Board: 2 copper layers, 90.0 x 90.0 mm, 21 parts (0 on the bottom side), 43 nets.

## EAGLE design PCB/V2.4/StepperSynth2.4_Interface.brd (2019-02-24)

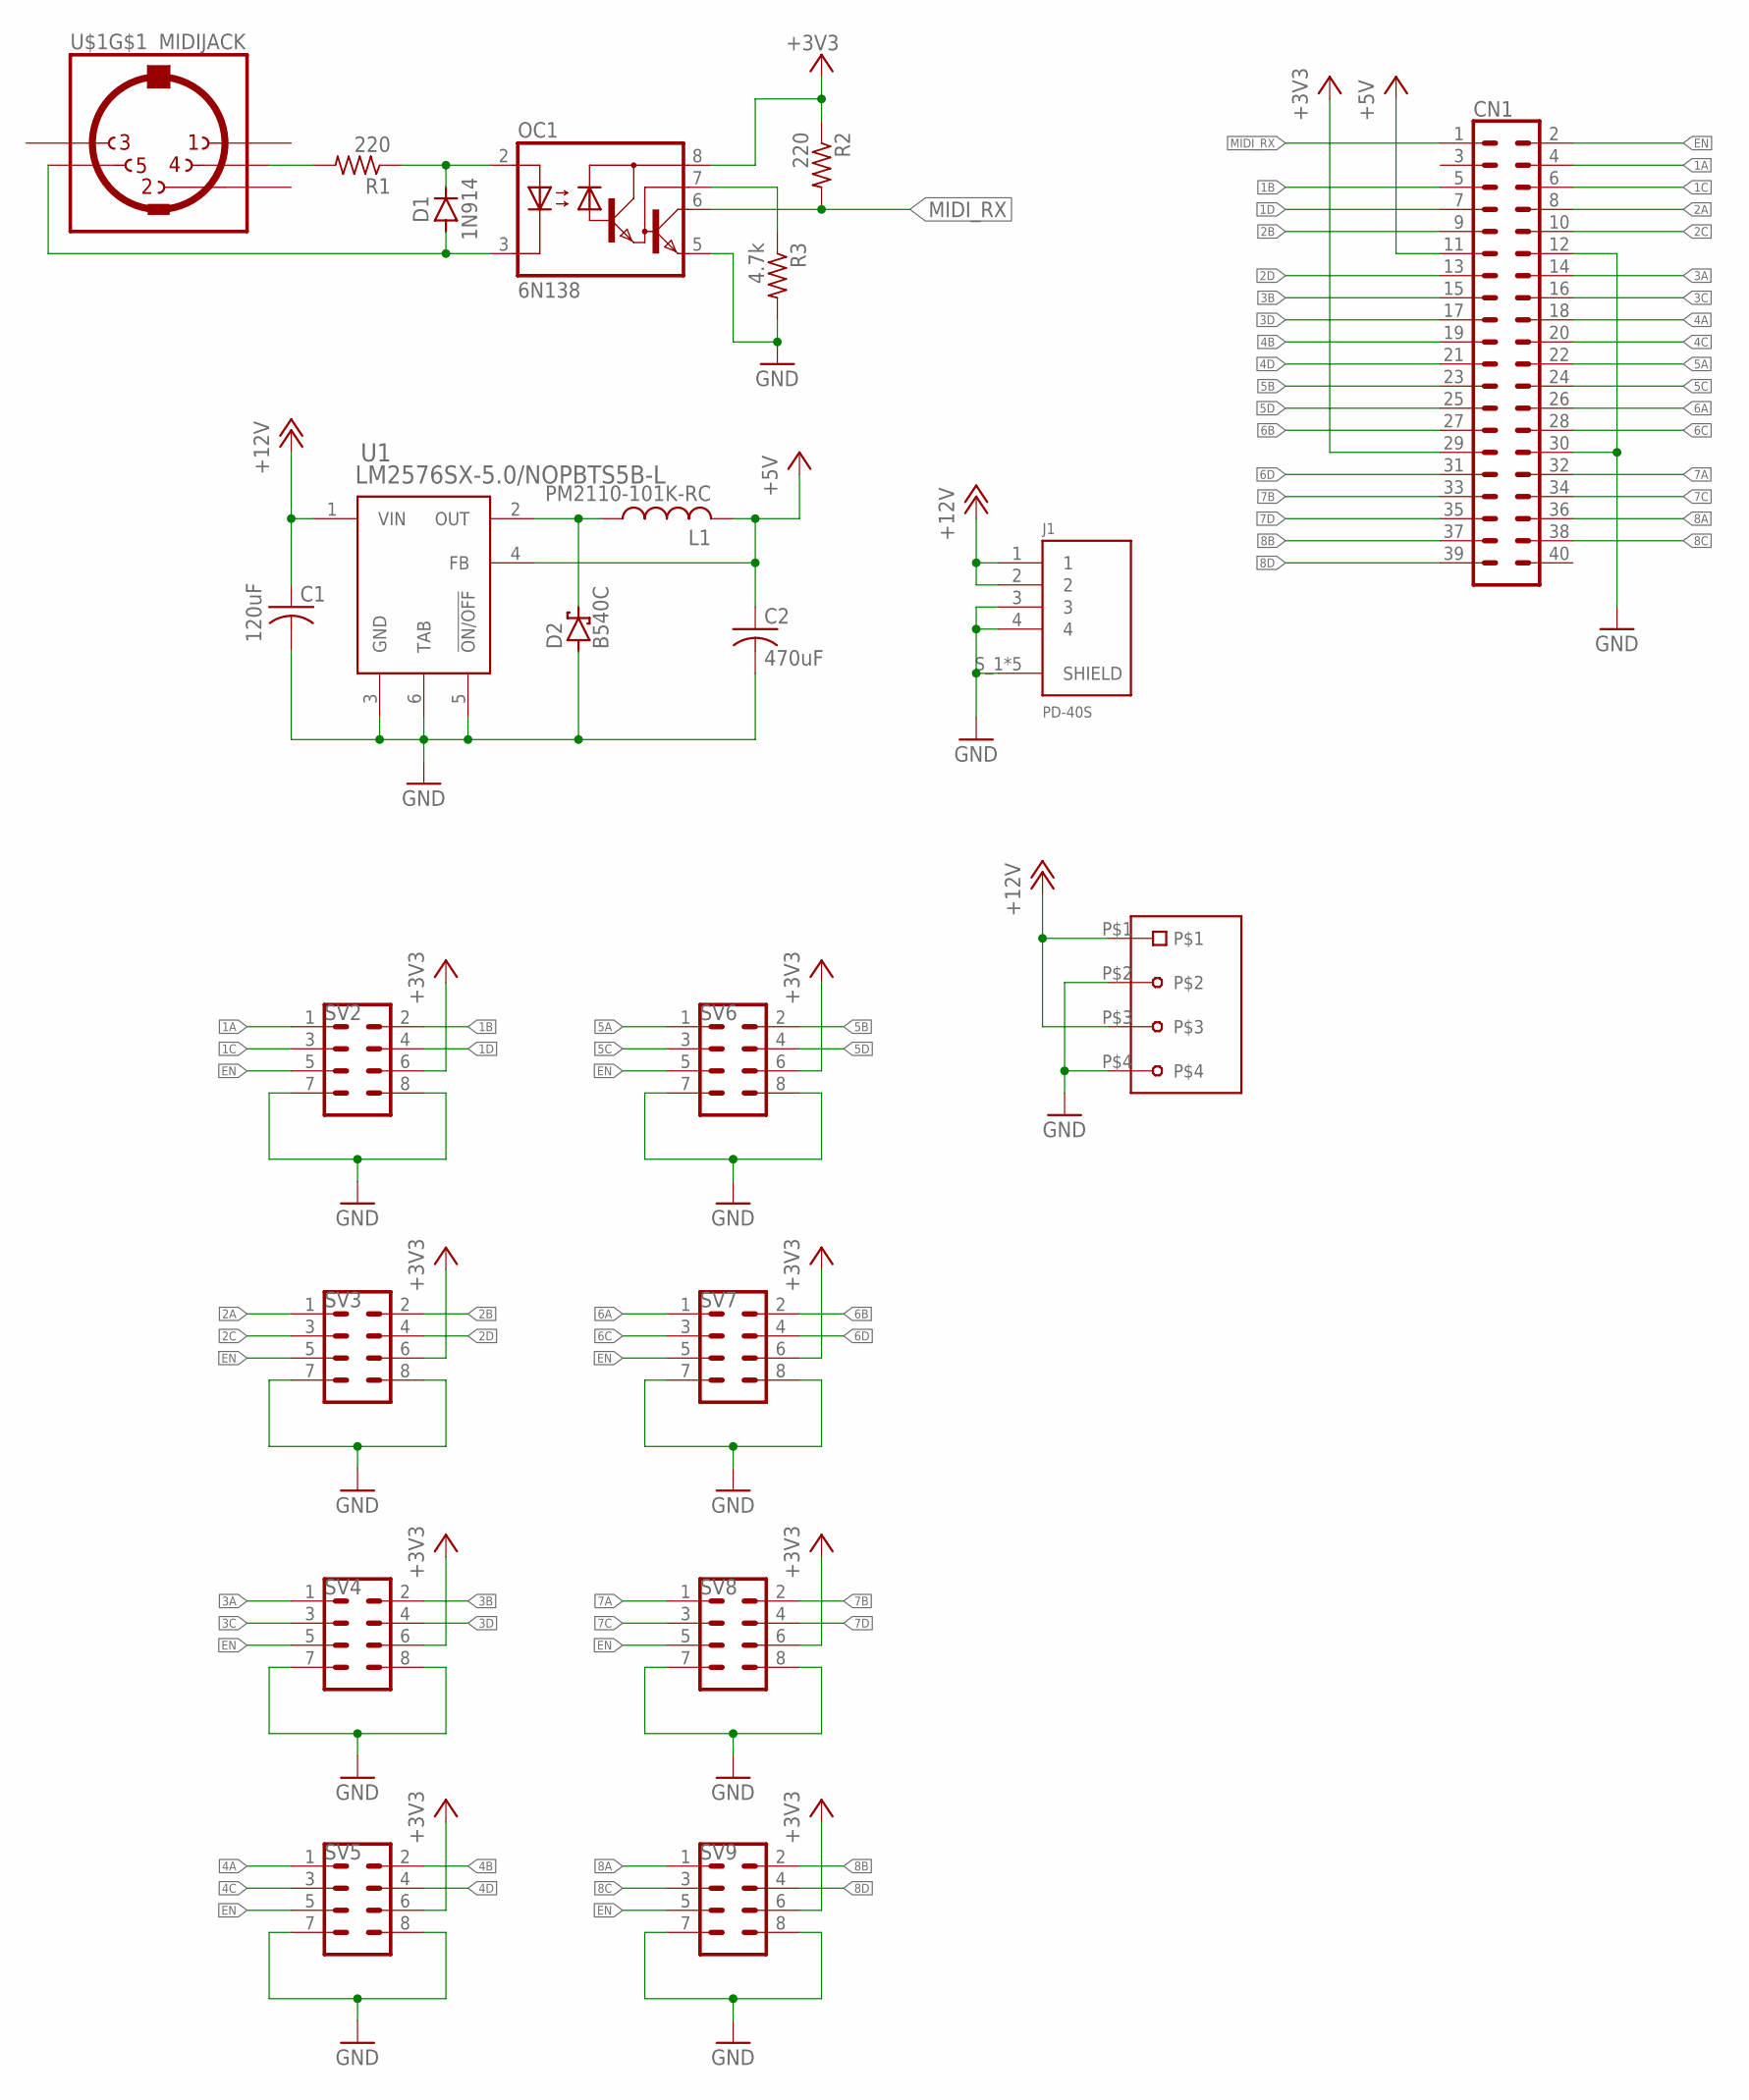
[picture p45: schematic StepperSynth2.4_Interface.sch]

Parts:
C1: 120uF; PCAP_SVP_C6-L
C2: 470uF; U2-P-L
CN1: CONN_20X2_LOCK; 1X20_LOCK
CN2: SCREW_TERMINAL_4POS_5MM; 4_POS-SCREW_TERM
D1: 1N914; DO35-7
D2: B540C; SMC
J1: PD-40S; CUI_PD-40S
L1: PM2110-101K-RC; IND_PM2110
OC1: 6N138; DIL08
R1, R2: 220; 0204/7
R3: 4.7k; 0204/7
SV2, SV3, SV4, SV5, SV6, SV7, SV8, SV9: CONN_4X2_LOCK; 1X04_LOCK
U1: LM2576SX-5.0/NOPBTS5B-L; TS5B-L
U$1: MIDIJACK; CP-2350

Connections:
1A: CN1.4, SV2.1
1B: CN1.5, SV2.2
1C: CN1.6, SV2.3
1D: CN1.7, SV2.4
2A: CN1.8, SV3.1
2B: CN1.9, SV3.2
2C: CN1.10, SV3.3
2D: CN1.13, SV3.4
3A: CN1.14, SV4.1
3B: CN1.15, SV4.2
3C: CN1.16, SV4.3
3D: CN1.17, SV4.4
4A: CN1.18, SV5.1
4B: CN1.19, SV5.2
4C: CN1.20, SV5.3
4D: CN1.21, SV5.4
5A: CN1.22, SV6.1
5B: CN1.23, SV6.2
5C: CN1.24, SV6.3
5D: CN1.25, SV6.4
6A: CN1.26, SV7.1
6B: CN1.27, SV7.2
6C: CN1.28, SV7.3
6D: CN1.31, SV7.4
7A: CN1.32, SV8.1
7B: CN1.33, SV8.2
7C: CN1.34, SV8.3
7D: CN1.35, SV8.4
8A: CN1.36, SV9.1
8B: CN1.37, SV9.2
8C: CN1.38, SV9.3
8D: CN1.39, SV9.4
+3V3: CN1.29, OC1.8 (VCC), R2.1, SV2.6, SV3.6, SV4.6, SV5.6, SV6.6, SV7.6, SV8.6, SV9.6
+5V: C2.1 (+), CN1.11, L1.2, U1.4 (FB)
+12V: C1.1 (+), CN2.P$1, CN2.P$3, J1.1, J1.2, U1.1 (VIN)
EN: CN1.2, SV2.5, SV3.5, SV4.5, SV5.5, SV6.5, SV7.5, SV8.5, SV9.5
GND: C1.2 (-), C2.2 (-), CN1.12, CN1.30, CN2.P$2, CN2.P$4, D2.A, J1.3, J1.4, J1.S_1 (SHIELD), J1.S_2 (SHIELD), J1.S_3 (SHIELD), J1.S_4 (SHIELD), J1.S_5 (SHIELD), OC1.5 (GND), R3.2, SV2.7, SV2.8, SV3.7, SV3.8, SV4.7, SV4.8, SV5.7, SV5.8, SV6.7, SV6.8, SV7.7, SV7.8, SV8.7, SV8.8, SV9.7, SV9.8, U1.3 (GND), U1.5 (!ON/OFF), U1.6 (TAB)
MIDI_RX: CN1.1, OC1.6 (VO), R2.2
unnamed: R1.2, U$1.4
unnamed: D1.C, OC1.2 (A), R1.1
unnamed: D1.A, OC1.3 (C), U$1.5
unnamed: OC1.7 (VB), R3.1
unnamed: D2.C, L1.1, U1.2 (OUT)

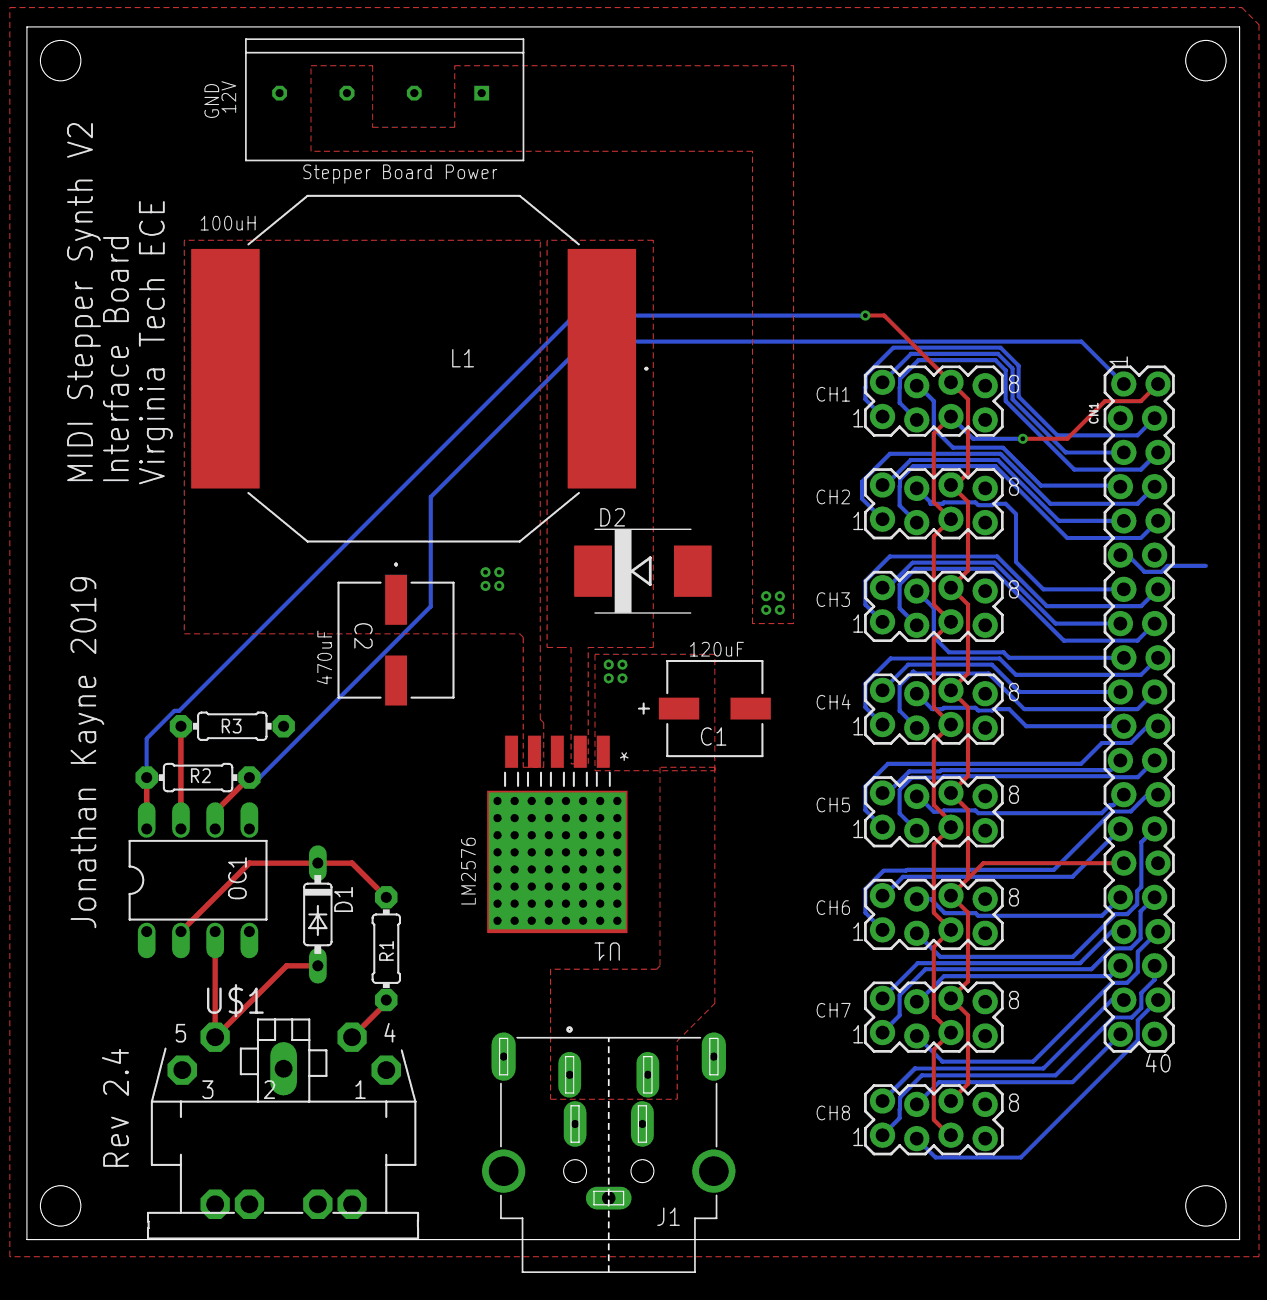
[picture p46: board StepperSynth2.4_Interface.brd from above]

Board: 2 copper layers, 90.0 x 92.4 mm, 22 parts (0 on the bottom side), 43 nets.

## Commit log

2019-02-02 Updated LED Switch control
2019-02-09 Renamed to SolidWorks
    [1x4 Male Header.SLDPRT, 1x8 Female Header.SLDPRT, 2x4 Male Header.SLDPRT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]
2019-02-24 Added V2.4
    [StepperSynth2.3_Interface.brd, StepperSynth2.3_Interface.sch, StepperSynth2.3_Motor.brd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]
2019-04-19 Added BOM Spreadsheet
    Includes a CSV for direct upload to Digikey
    [Digikey_BOM.csv, MIDI Synth V2 BOM.xlsx]
2019-04-23 Fixed BOM
    [MIDI Synth V2 BOM.xlsx]
